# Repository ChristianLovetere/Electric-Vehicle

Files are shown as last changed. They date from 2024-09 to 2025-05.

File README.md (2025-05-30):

In this project, we use Dahlander motor technology via mechanical relays to alter the torque / speed of the electric vehicle. A custom PCB is used to route all the wiring connections from the Arduino MEGA to the RF Receiver, relays, battery, and motor / motor controllers.

<p align="center">
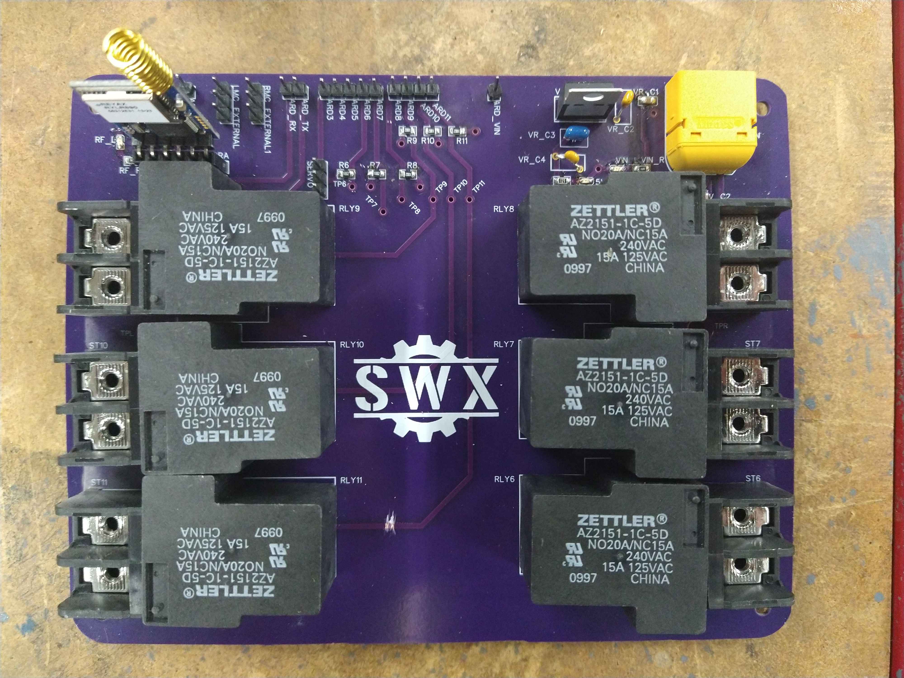
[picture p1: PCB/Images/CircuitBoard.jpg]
  
</p>

The PCB is a 4-layer design consisting of a Signal-Ground-Power-Signal stackup. The top and bottom (signal) layers can be seen below:

<p align="center">
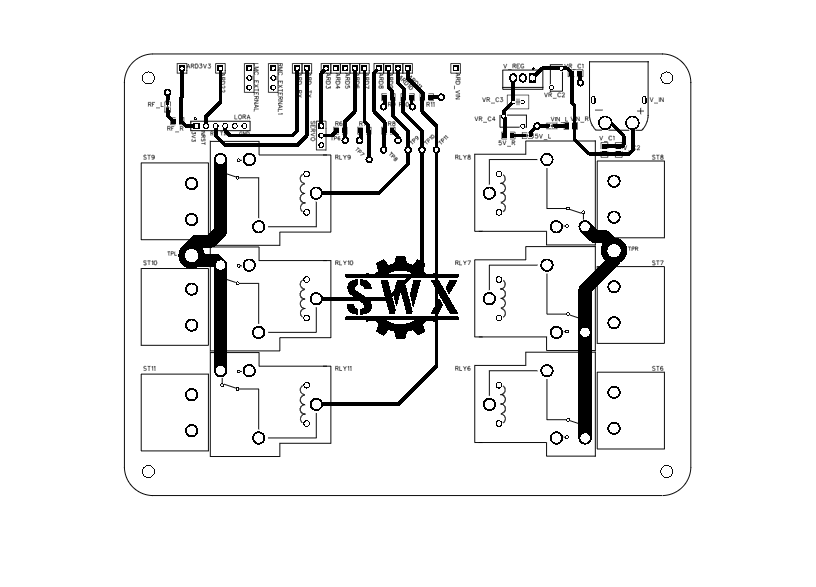
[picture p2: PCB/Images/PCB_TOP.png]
  
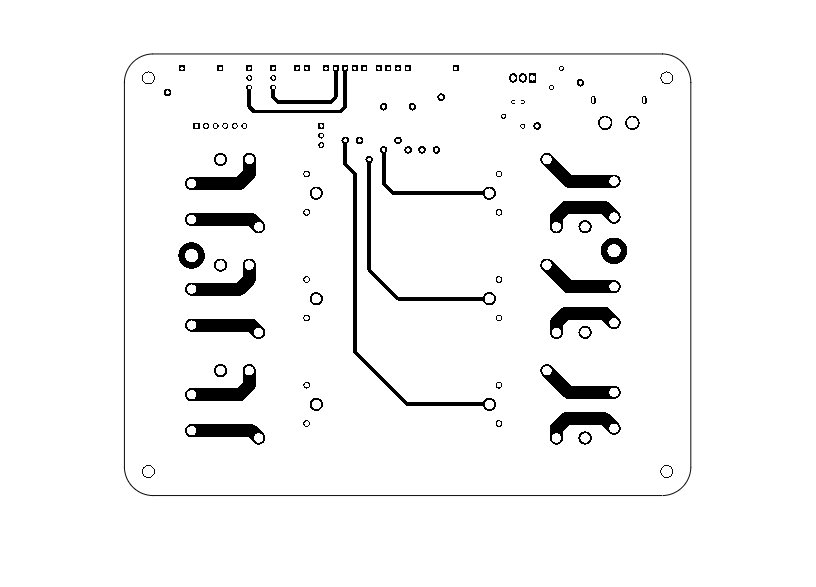
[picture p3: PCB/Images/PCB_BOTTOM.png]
  
</p>

This schematic shows the different aspects of the design. VCC is used to denote the power source (likely a 3S to 5S Lithium Polymer battery). A 7805L is used to drop the battery voltage down to 5V for delivery to the majority of the other components. The 3.3v required to power the REYAX RYLR896 (RF module) is acquired from the 3v3 pin on the Arduino, because the current supplied by this pin is enough to power the module without any trouble.
<p align="center">
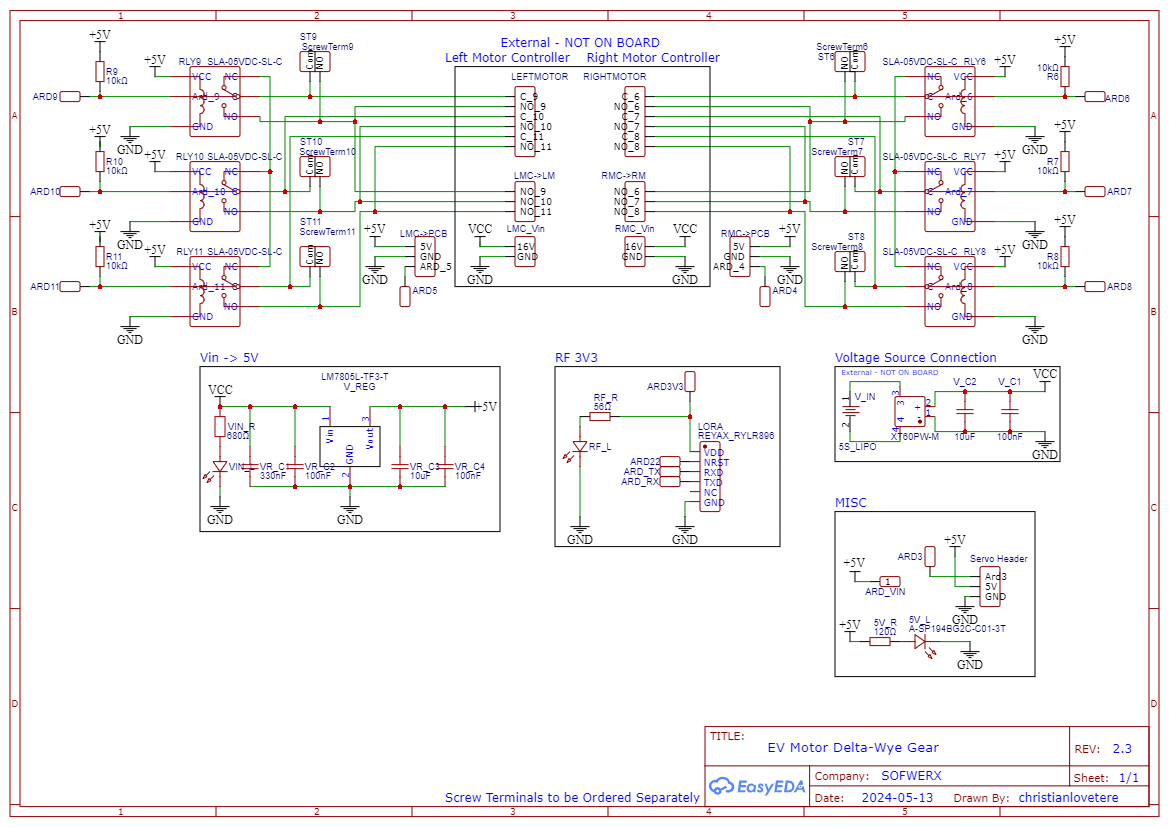
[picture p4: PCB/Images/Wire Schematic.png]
  
</p>

Portable Controller subproject has its own readme in the Portable Controller folder.

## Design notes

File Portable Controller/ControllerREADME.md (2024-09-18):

A subproject of the car project. This portable controller has a power on/off switch for ease of use and a USB-C charger slot so that it can be charged by any generic USB-C charger. It contains the REYAX RYLR896 RF module for transmitting to the Electric Vehicle, an HD44780 LCD screen with I2C backpack, raspberry pi 3, 5V 2.5A power bank, and a 3DConnexion SpaceMouse for input.

<p align="center">
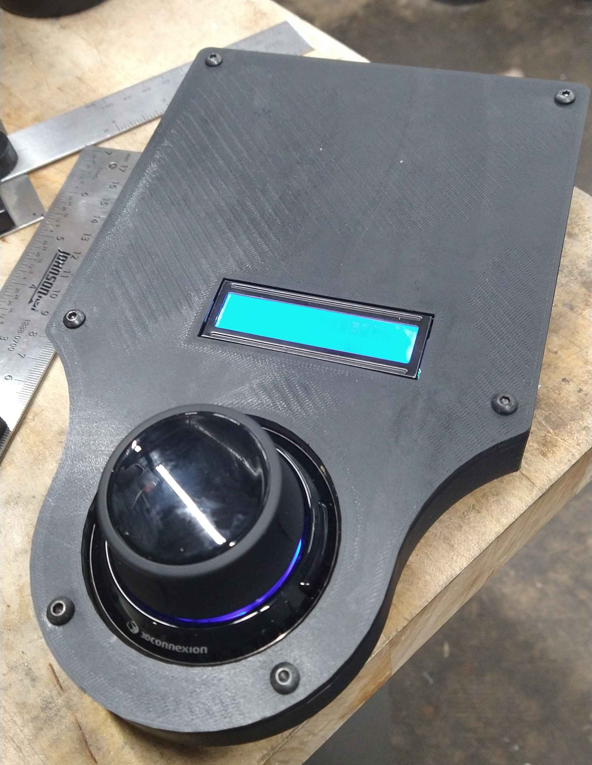
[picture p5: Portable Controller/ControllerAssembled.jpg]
  
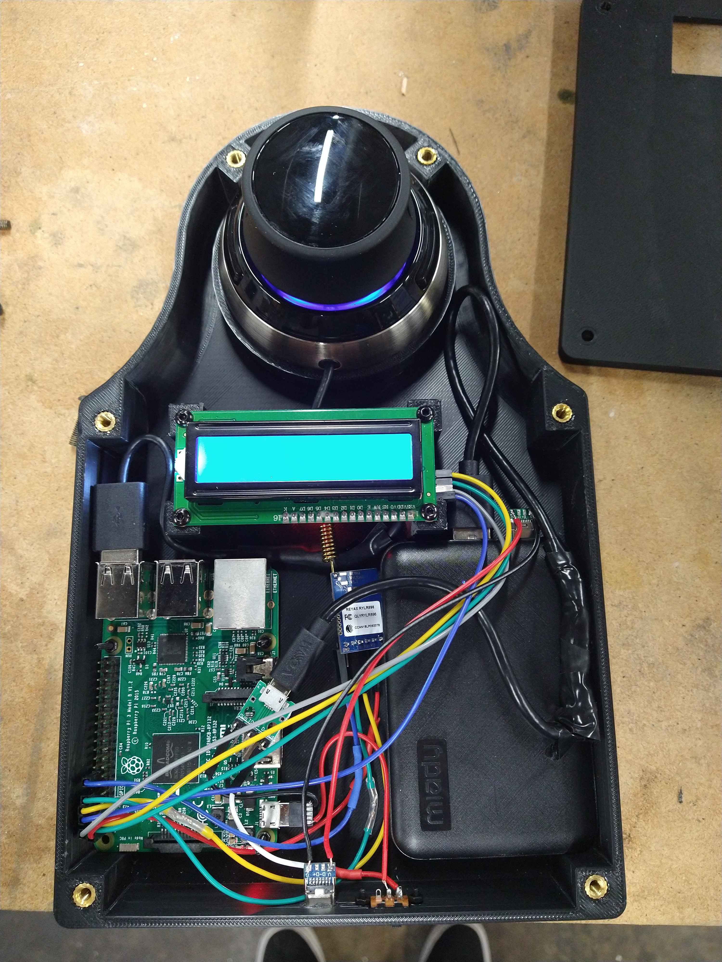
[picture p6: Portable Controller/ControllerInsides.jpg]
  
</p>

The LCD Screen displays the current left and right motor packet (intensity and direction) as well as a short string that demonstrates the intended action (slight left, hard right, drag turn, etc.)

The SpaceMouse is used to control the vehicle, rotating it left and right to indicate turning, and forward and backward for that. The side buttons are currently used to exit the program, but will eventually be used to flip the relays on the PCB and change gear for the vehicle.

Controller Schematic:

<p align="center">
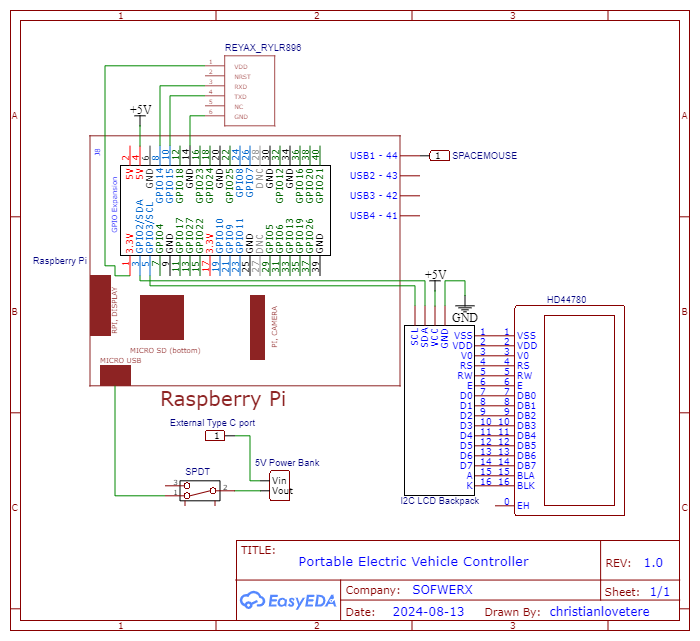
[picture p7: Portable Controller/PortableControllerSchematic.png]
What is this
  
</p>

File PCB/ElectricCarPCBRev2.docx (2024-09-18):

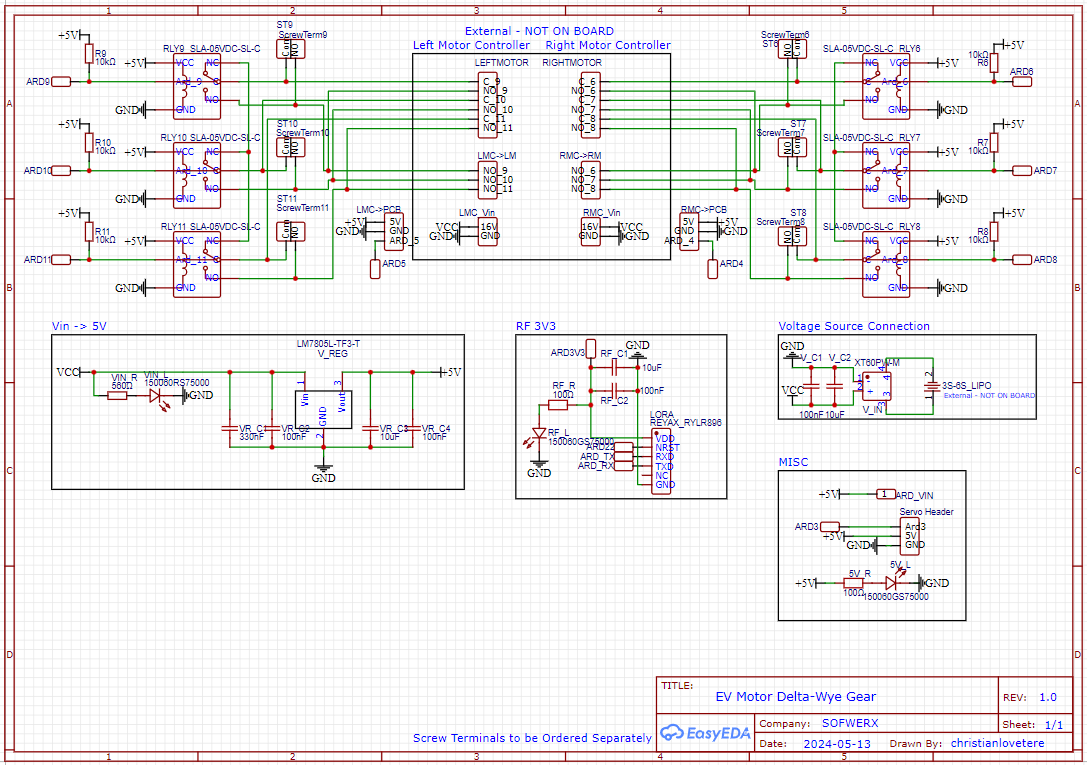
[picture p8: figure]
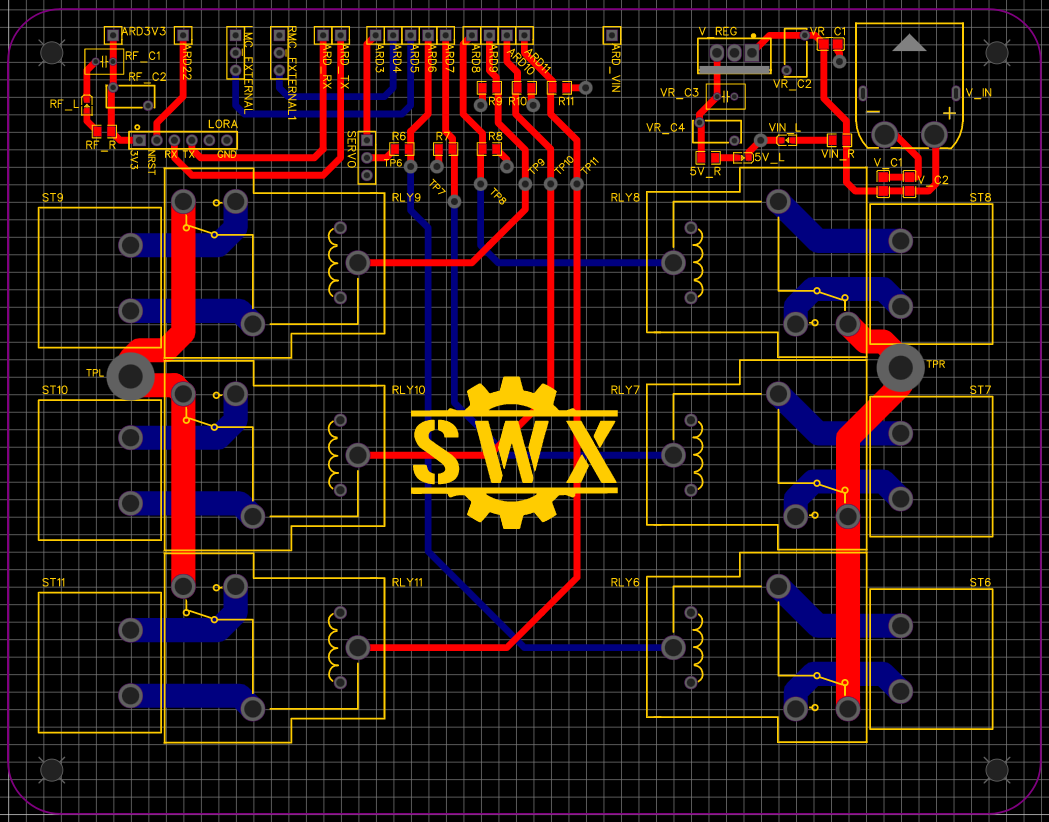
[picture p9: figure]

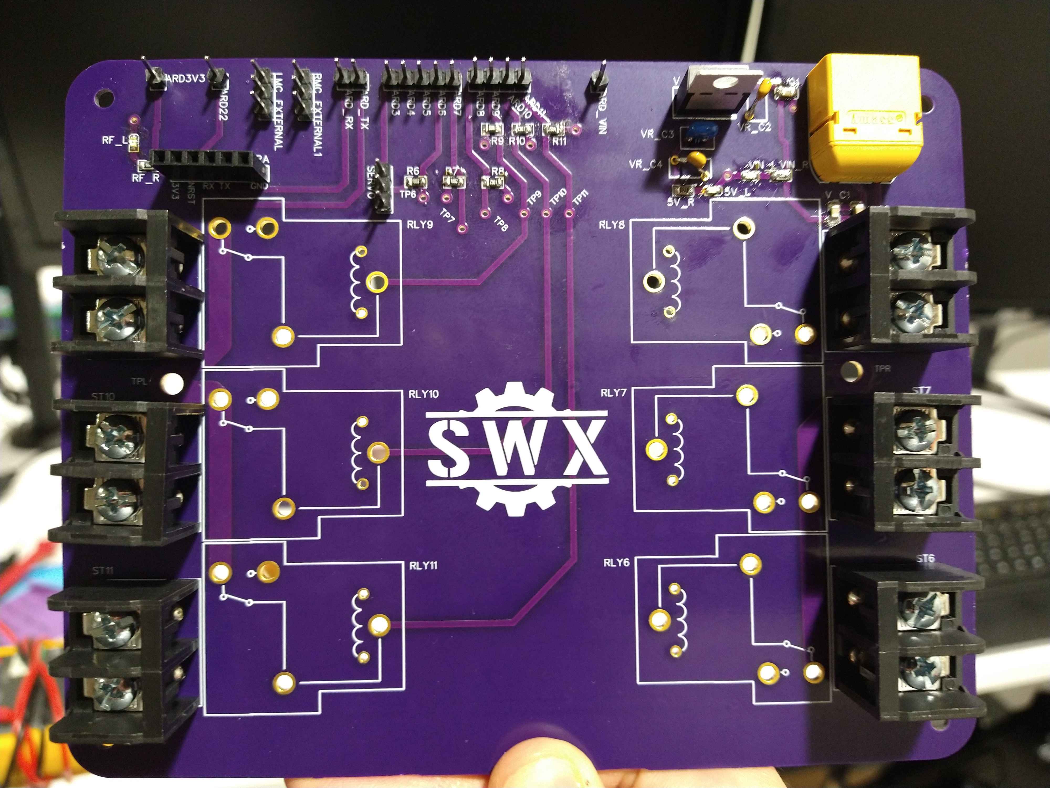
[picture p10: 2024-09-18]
PCB/Images/CircuitBoard2.jpg

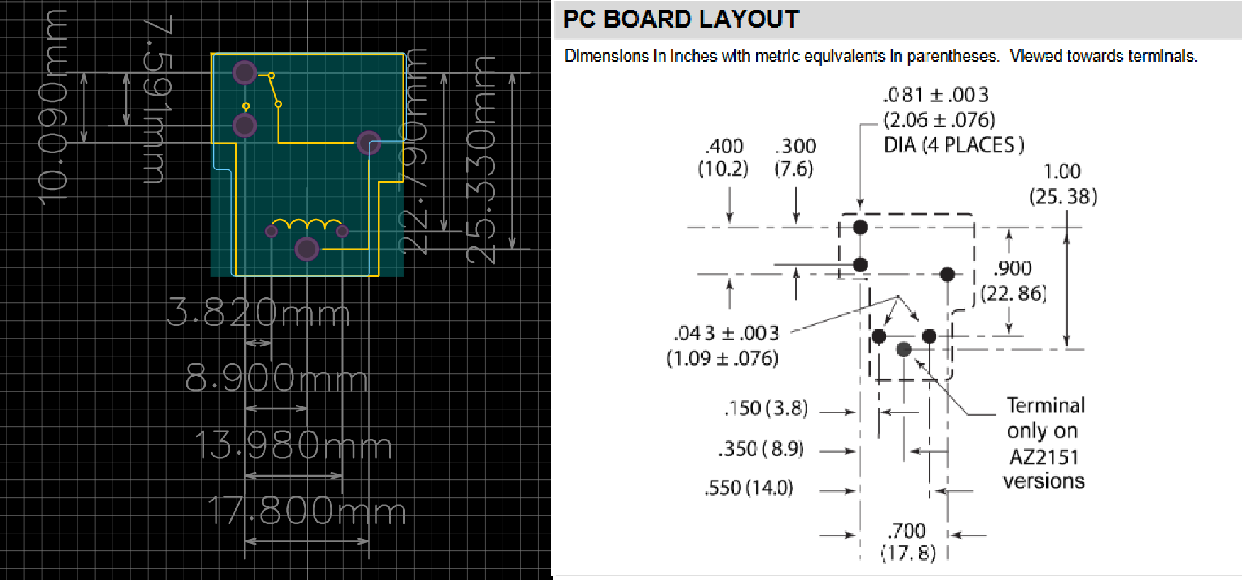
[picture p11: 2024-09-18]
Part Selection/american vs chinese relay.png

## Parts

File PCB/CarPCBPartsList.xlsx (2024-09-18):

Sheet: BOM_Electric-Car-PCB_2024-07-02
ID | Ordered | Replacement Found | Already Owned | On Board? | Name | Designator | Footprint | Quantity | Manufacturer Part | Manufacturer | Supplier | Supplier Part | Price | Link
1 |  |  | x |  | >16V | 5S_LIPO | BAT-SMD_CR1220-2 | 1 | CR1220-2 | Q&J | LCSC
2 | x |  |  | x | A-SP194BG2C-C01-3T | 5V_L,RF_L,VIN_L | LED0603-RD | 3 | A-SP194BG2C-C01-3T | Amicc(欧密格光电) | LCSC | C5179616 | 0.023 | https://jlcpcb.com/partdetail/Amicc-A_SP194BG2C_C013T/C5179616
3 |  | x |  | x | 120Ω | 5V_R | R0805 | 1 | RS-05K1200FT | FH(风华) | LCSC | C139926 | 0.002 | https://www.lcsc.com/datasheet/lcsc_datasheet_2304140030_FH--Guangdong-Fenghua-Advanced-Tech-RS-05K1200FT_C139926.pdf
4 |  | x |  | x | ARD3 | ARD3 | HDR-M-2.54_1X1 | 1 |  |  | LCSC | C81276 | 0.007 | -
5 |  | x |  | x | ARD3V3 | ARD3V3 | HDR-M-2.54_1X1 | 1 |  |  | LCSC | C81276 | 0.007 | -
6 |  | x |  | x | ARD4 | ARD4 | HDR-M-2.54_1X1 | 1 |  |  | LCSC | C81276 | 0.007 | -
7 |  | x |  | x | ARD5 | ARD5 | HDR-M-2.54_1X1 | 1 |  |  | LCSC | C81276 | 0.007 | -
8 |  | x |  | x | ARD6 | ARD6 | HDR-M-2.54_1X1 | 1 |  |  | LCSC | C81276 | 0.007 | -
9 |  | x |  | x | ARD7 | ARD7 | HDR-M-2.54_1X1 | 1 |  |  | LCSC | C81276 | 0.007 | -
10 |  | x |  | x | ARD8 | ARD8 | HDR-M-2.54_1X1 | 1 |  |  | LCSC | C81276 | 0.007 | -
11 |  | x |  | x | ARD9 | ARD9 | HDR-M-2.54_1X1 | 1 |  |  | LCSC | C81276 | 0.007 | -
12 |  | x |  | x | ARD10 | ARD10 | HDR-M-2.54_1X1 | 1 |  |  | LCSC | C81276 | 0.007 | -
13 |  | x |  | x | ARD11 | ARD11 | HDR-M-2.54_1X1 | 1 |  |  | LCSC | C81276 | 0.007 | -
14 |  | x |  | x | ARD22 | ARD22 | HDR-M-2.54_1X1 | 1 |  |  | LCSC | C81276 | 0.007 | -
15 |  | x |  | x | ARD_RX | ARD_RX | HDR-M-2.54_1X1 | 1 |  |  | LCSC | C81276 | 0.007 | -
16 |  | x |  | x | ARD_TX | ARD_TX | HDR-M-2.54_1X1 | 1 |  |  | LCSC | C81276 | 0.007 | -
17 |  | x |  | x | ARD_VIN | ARD_VIN | HDR-M-2.54_1X1 | 1 |  |  | LCSC | C81276 | 0.007 | -
18 |  |  |  |  | LEFTMOTOR | LEFTMOTOR | HDR-M-2.54_1X6 | 1 |  |  | LCSC | C190819 | 0.029
19 |  |  |  |  | LMC_Vin | LMCPOWER | HDR-M-2.54_1X2 | 1 |  |  | LCSC | C124375 | 0.023
20 |  | x |  | x | LMC->PCB | LMC_EXTERNAL | HDR-M-2.54_1X3 | 1 |  |  | LCSC | C180248 | 0.181 | -
21 |  |  |  |  | LMC->LM | LMC_INTERNAL | HDR-M-2.54_1X3 | 1 |  |  | LCSC | C180248 | 0.181
22 |  |  | x | x | REYAX_RYLR896 | LORA | HDR-TH_6P-P2.54-V-F | 1 | 2.54-1*6P母 | BOOMELE(博穆精密) | LCSC | C40877 | 0.071
23 | x |  |  | x | 10kΩ | R6,R7,R8,R9,R10,R11 | R0805 | 6 | RC0805FR-0710KL | YAGEO(国巨) | LCSC | C84376 | 0.002 | https://www.digikey.com/en/products/detail/yageo/RC0805FR-0710KL/727535
24 | x |  |  | x | 56Ω | RF_R | R0805 | 1 | 0805W8J0560T5E | UNI-ROYAL(厚声) | LCSC | C25320 | 0.001 | https://www.lcsc.com/product-detail/Chip-Resistor-Surface-Mount_Uniroyal-Elec-0805W8J0560T5E_C25320.html
25 |  |  |  |  | RIGHTMOTOR | RIGHTMOTOR | HDR-M-2.54_1X6 | 1 |  |  | LCSC | C190819 | 0.029
26 |  | x |  | x | SLA-05VDC-SL-C | RLY6,RLY7,RLY8,RLY9,RLY10,RLY11 | RELAY-TH_SLA-XXVDC-XX-C | 6 | SLA-05VDC-SL-C | 松乐 | LCSC | C87367 | 0.928 | https://www.lcsc.com/product-detail/Power-Relays_Ningbo-Songle-Relay-SLA-05VDC-SL-C_C87367.html
27 |  |  |  |  | RMC_Vin | RMCPOWER | HDR-M-2.54_1X2 | 1 |  |  | LCSC | C124375 | 0.023
28 |  | x |  | x | RMC->PCB | RMC_EXTERNAL1 | HDR-M-2.54_1X3 | 1 |  |  | LCSC | C180248 | 0.181 | -
29 |  |  |  |  | RMC->RM | RMC_INTERNAL1 | HDR-M-2.54_1X3 | 1 |  |  | LCSC | C180248 | 0.181
30 |  | x |  | x | Servo Header | SERVO | HDR-M-2.54_1X3 | 1 |  |  | LCSC | C180248 | 0.181 | -
31 | x |  |  | x | ScrewTerm6 | ST6 | TERMINAL_BLOCK_2 | 1 | 6PCV-02-006 |  | LCSC | C124375 | 0.023 | https://www.digikey.com/en/products/detail/te-connectivity-amp-connectors/6PCV-02-006/1277933
32 | x |  |  | x | ScrewTerm7 | ST7 | TERMINAL_BLOCK_2 | 1 | 6PCV-02-006 |  | LCSC | C124375 | 0.023 | https://www.digikey.com/en/products/detail/te-connectivity-amp-connectors/6PCV-02-006/1277934
33 | x |  |  | x | ScrewTerm8 | ST8 | TERMINAL_BLOCK_2 | 1 | 6PCV-02-006 |  | LCSC | C124375 | 0.023 | https://www.digikey.com/en/products/detail/te-connectivity-amp-connectors/6PCV-02-006/1277935
34 | x |  |  | x | ScrewTerm9 | ST9 | TERMINAL_BLOCK_2 | 1 | 6PCV-02-006 |  | LCSC | C124375 | 0.023 | https://www.digikey.com/en/products/detail/te-connectivity-amp-connectors/6PCV-02-006/1277936
35 | x |  |  | x | ScrewTerm10 | ST10 | TERMINAL_BLOCK_2 | 1 | 6PCV-02-006 |  | LCSC | C124375 | 0.023 | https://www.digikey.com/en/products/detail/te-connectivity-amp-connectors/6PCV-02-006/1277937
36 | x |  |  | x | ScrewTerm11 | ST11 | TERMINAL_BLOCK_2 | 1 | 6PCV-02-006 |  | LCSC | C124375 | 0.023 | https://www.digikey.com/en/products/detail/te-connectivity-amp-connectors/6PCV-02-006/1277938
37 | x |  |  | x | 680Ω | VIN_R | R0805 | 1 | CR0805F680RP05Z | EVER OHMS(天二科技) | LCSC | C880974 | 0.003 | https://jlcpcb.com/kr/partdetail/Ever_OhmsTech-CR0805F680RP05Z/C880974
38 | x |  |  | x | 330nF | VR_C1 | C0805 | 1 | GCJ219R71H334KA12D | muRata(村田) | LCSC | C527609 | 0.091 | https://www.digikey.com/en/products/detail/murata-electronics/GCJ219R71H334KA12D/6606042
39 |  | x |  | x | 100nF | VR_C2,VR_C4 | CAP-TH_L7.0-W3.2-P5.08-D0.6-S2.7 | 2 | CC2A104ZC1ED3F7C1100 | Dersonic(德尔创) | LCSC | C2761731 | 0.02 | https://www.lcsc.com/product-detail/Ceramic-Disc-Capacitors_Dersonic-CC2A104ZC1ED3F7C1100_C2761731.html
 | x |  |  | x | 10uF | VR_C3 | CAP-TH_L5.5-W3.5-P2.50-D0.5 | 1 | FK16X7R1C106K | TDK | LCSC | C3689076 | 0.142 | https://www.digikey.com/en/products/detail/tdk-corporation/FK16X7R1C106KR020/2815278
41 | x |  |  | x | 100nF | V_C1 | C0805 | 1 | CC0805KRX7R8BB104 | YAGEO(国巨) | LCSC | C519981 | 0.006 | https://www.digikey.com/en/products/detail/yageo/CC0805KRX7R8BB104/302875
42 |  | x |  | x | 10uF | V_C2 | C0805 | 1 | TCC0805X5R106K100FT | CCTC(三环) | LCSC | C380331 | 0.009 | https://jlcpcb.com/partdetail/CCTC-TCC0805X5R106K100FT/C380331
43 | x |  |  | x | XT60PW-M | V_IN | CONN-TH_XT60PW-M | 1 | XT60PW-M | AMASS(艾迈斯) | LCSC | C98732 | 0.388 | https://www.tme.com/us/en-us/details/xt60pw-m/dc-power-connectors/amass/
44 | x |  | x | x | LM7805L-TF3-T | V_REG | TO-220F-3_L10.2-W4.9-P2.54-L | 1 | LM7805L-TF3-T | UTC(友顺) | LCSC | C71107 | 0.216 | https://www.digikey.com/en/products/base-product/onsemi/488/LM7805/17942

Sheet: Digikey Part Replacements
Old Part | New Part Link | Quantity | Works For
HDR-M-2.54_1X1 | https://www.digikey.com/en/products/detail/w%C3%BCrth-elektronik/61300111121/4846821 | 3 | ARD3V3, ARD22, ARD_VIN
HDR-M-2.54_1X2 | https://www.digikey.com/en/products/detail/w%C3%BCrth-elektronik/61300211121/4846823 | 1 | ARD_RX, ARD_TX
HDR-M-2.54_1X3 | https://www.digikey.com/en/products/detail/w%C3%BCrth-elektronik/61300311121/4846825 | 3 | LMC_External, RMC_External, Servo Header
HDR-M-2.54_1X4 | https://www.digikey.com/en/products/detail/w%C3%BCrth-elektronik/61300411121/4846827 | 1 | ARD8-11
HDR-M-2.54_1X5 | https://www.digikey.com/en/products/detail/w%C3%BCrth-elektronik/61300511121/4846831 | 1 | ARD3-7
CC2A104ZC1ED3F7C1100 | https://www.digikey.com/en/products/detail/vishay-beyschlag-draloric-bc-components/K104K10X7RF5UH5/2356754 | 2 | VR_C2, VR_C4
TCC0805X5R106K100FT | https://www.digikey.com/en/products/detail/cal-chip-electronics-inc/GMC21X7R106K25NT/22639515 | 1 | V_C2
SLA-05VDC-SL-C | https://www.e-sonic.com/en/productdetail/american-zettler/az21511a5de-10610544.html | 6 | RLY6-11
 | https://www.masterelectronics.com/en/productdetail/american-zettler/az21511a5de-10610544.html
RS-05K1200FT | https://www.digikey.com/en/products/detail/susumu/RG2012N-121-W-T1/600666 | 1 | 5V_R

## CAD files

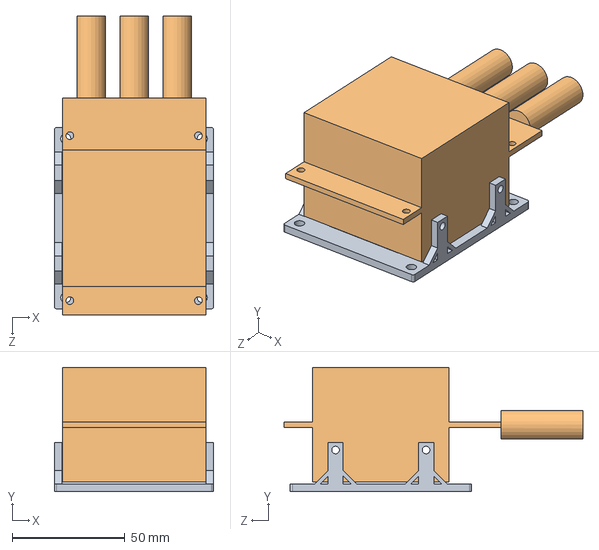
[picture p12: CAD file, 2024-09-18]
3D Modeling/MotorControllerFit.SLDASM
70.4 x 55.1 x 132.4 mm
MotorController
MotorControllerMount

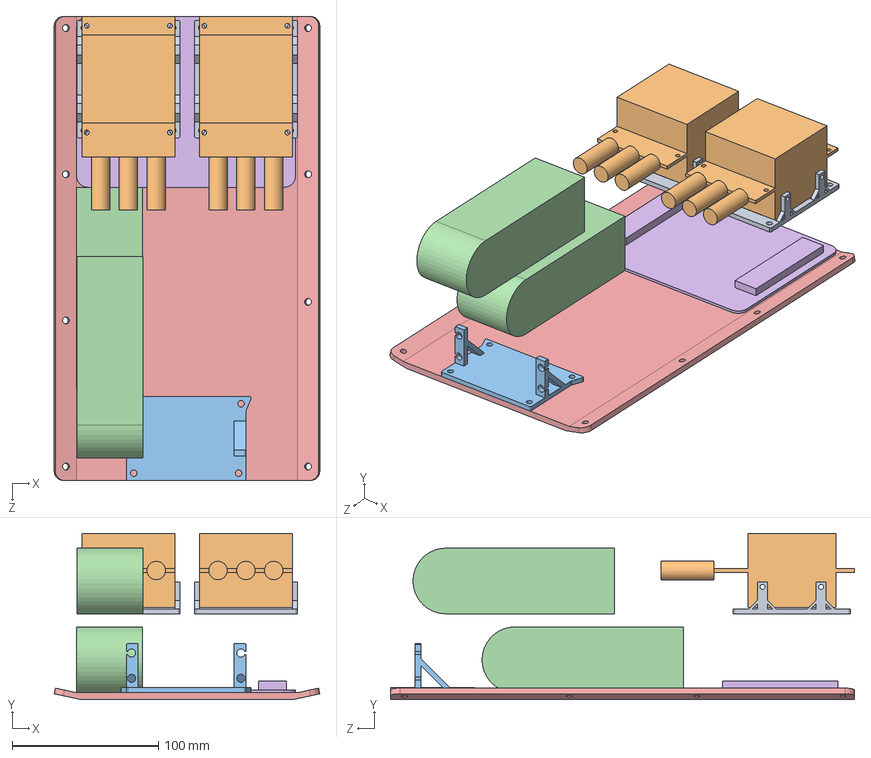
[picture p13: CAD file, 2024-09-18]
3D Modeling/ElecCarAssembly.SLDASM
181.8 x 113.8 x 317.5 mm
PCB
VehicleBase
6s LiPo x 2
ServoMount
MotorController x 2
MotorControllerMount x 2

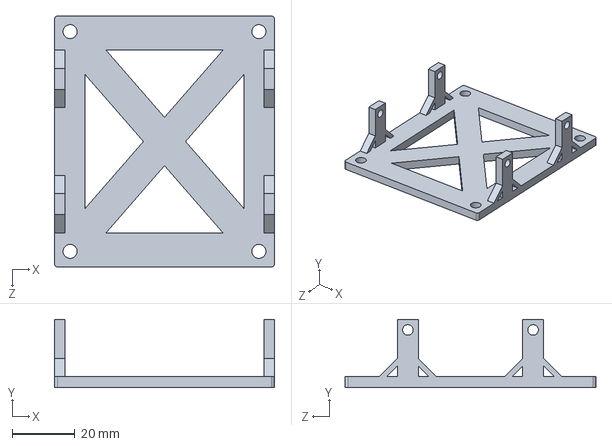
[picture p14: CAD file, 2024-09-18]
3D Modeling/MotorControllerMount.SLDPRT
70.4 x 21.9 x 80.3 mm

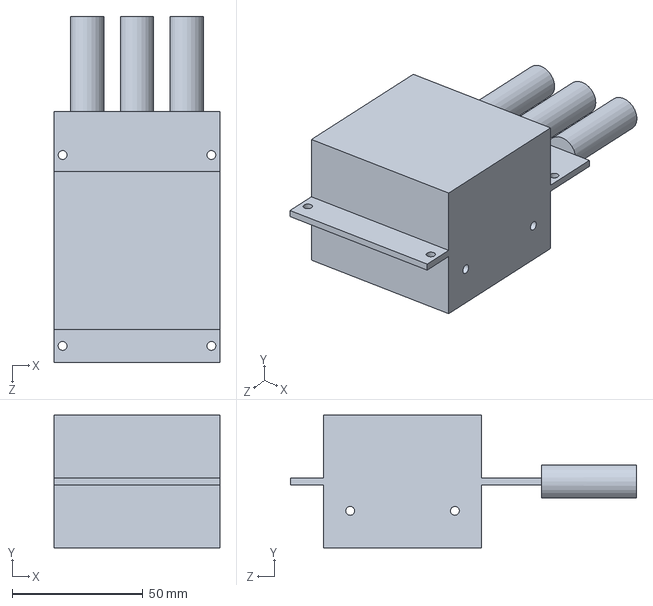
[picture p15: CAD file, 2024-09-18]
3D Modeling/MotorController.SLDPRT
63.5 x 50.8 x 132.4 mm

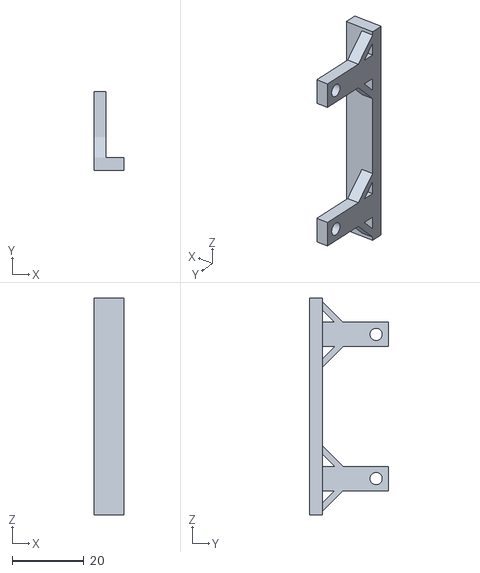
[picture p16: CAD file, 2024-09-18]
3D Modeling/MotorControllerMountTESTPART_2.STL
8.38 x 21.9 x 60.3

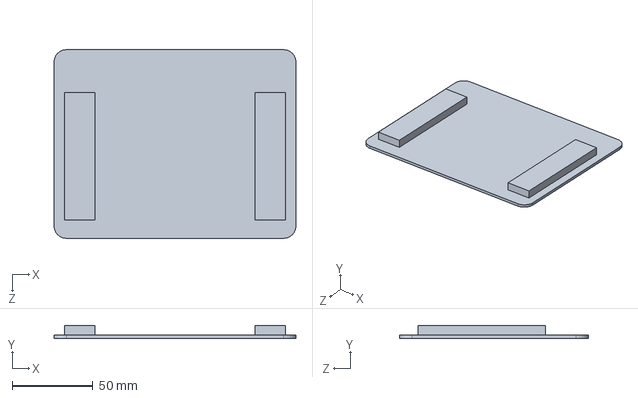
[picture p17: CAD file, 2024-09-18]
3D Modeling/PCB.SLDPRT
149.9 x 7.84 x 116.8 mm

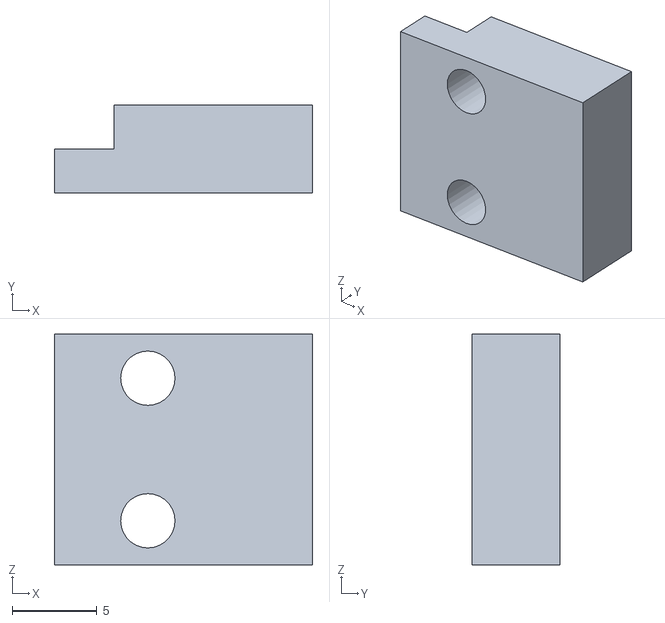
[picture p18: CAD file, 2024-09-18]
3D Modeling/micro usb pin cover.stl
15.2 x 5.20 x 13.6

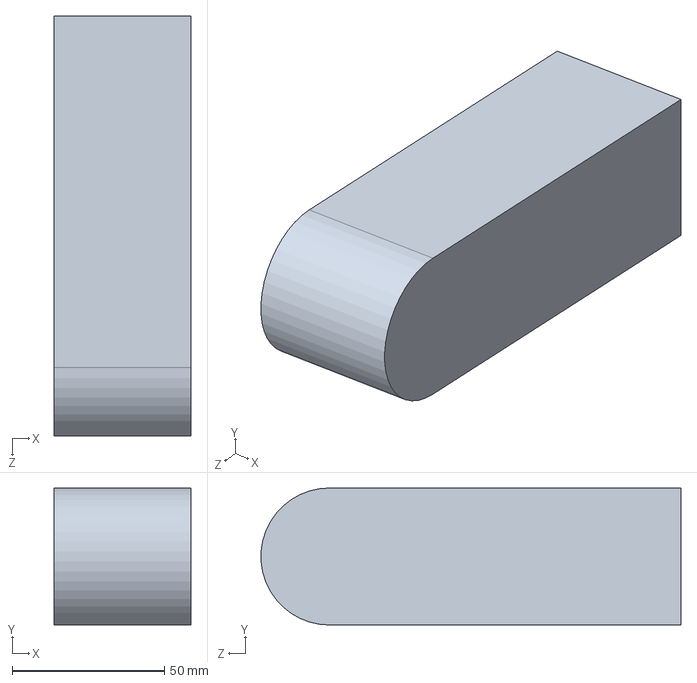
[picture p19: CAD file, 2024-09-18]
3D Modeling/6s LiPo.SLDPRT
45.0 x 45.0 x 137.9 mm

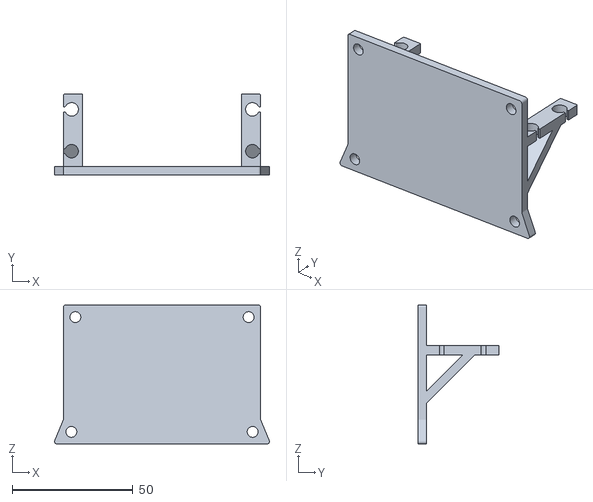
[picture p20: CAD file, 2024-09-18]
3D Modeling/ServoMountMK2.STL
89.0 x 33.5 x 57.5

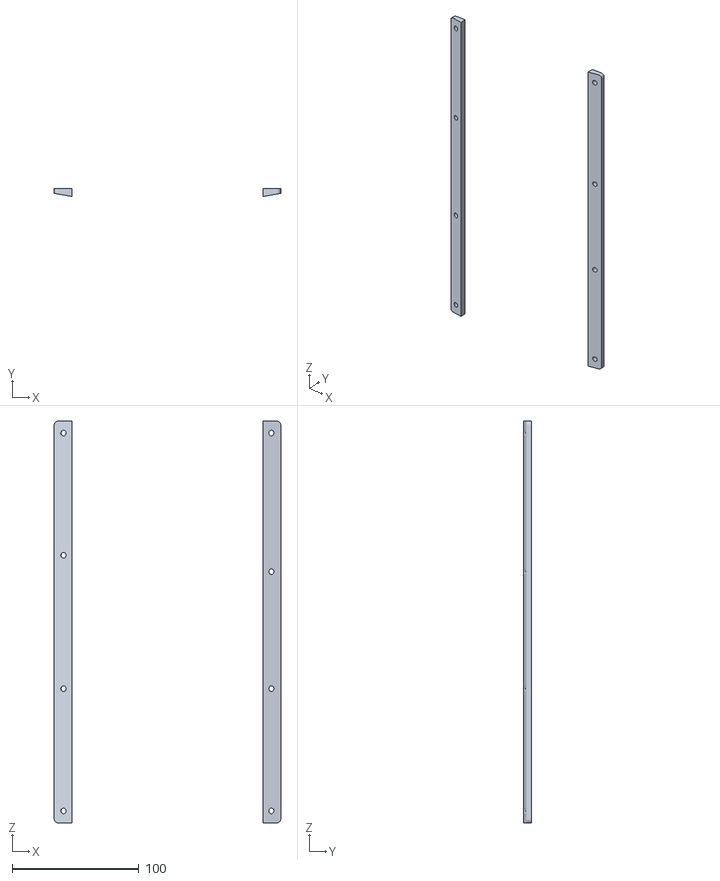
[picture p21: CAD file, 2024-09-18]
3D Modeling/VehicleChassisHoleAlignmentTestPart.STL
179.0 x 6.35 x 317.5

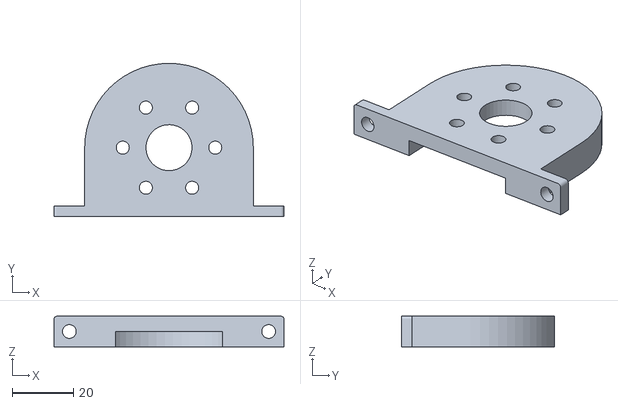
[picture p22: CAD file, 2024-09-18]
3D Modeling/MotorMountTESTPART_2.STL
75.0 x 50.0 x 10.0

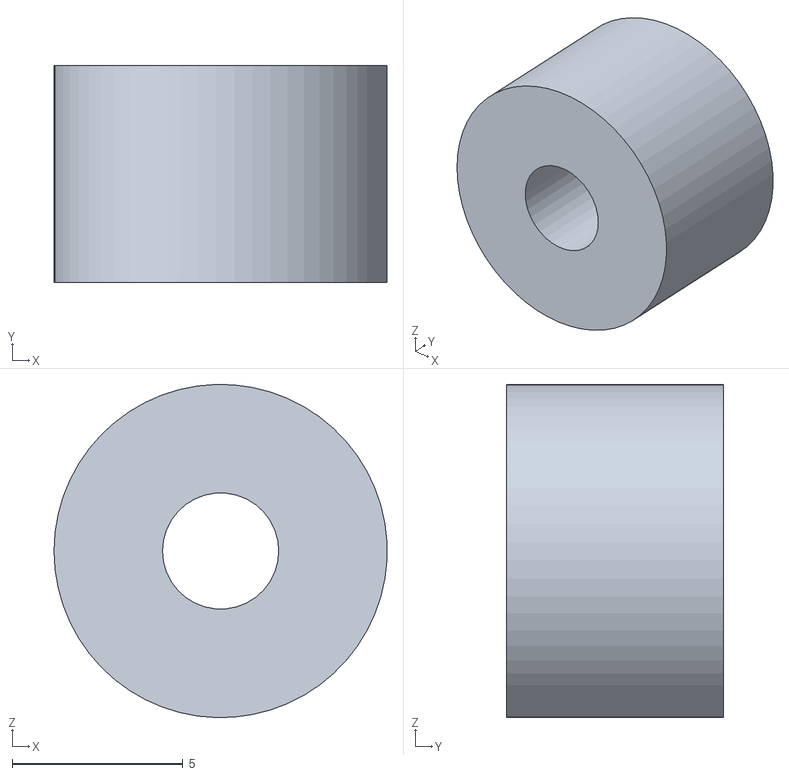
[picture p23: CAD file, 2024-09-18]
3D Modeling/spacer for mounting pcb.stl
9.74 x 6.35 x 9.75

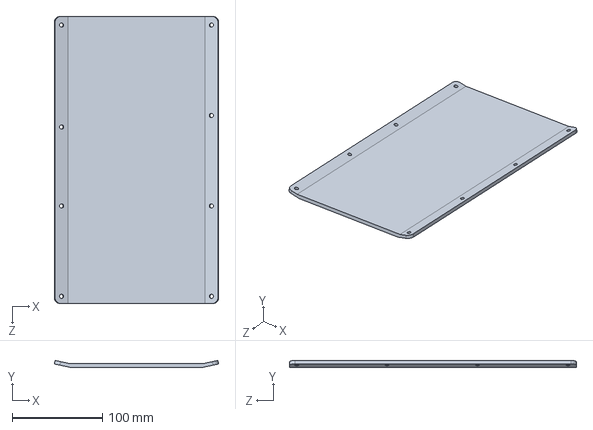
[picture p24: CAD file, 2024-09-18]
3D Modeling/VehicleBase.SLDPRT
181.8 x 7.89 x 317.5 mm

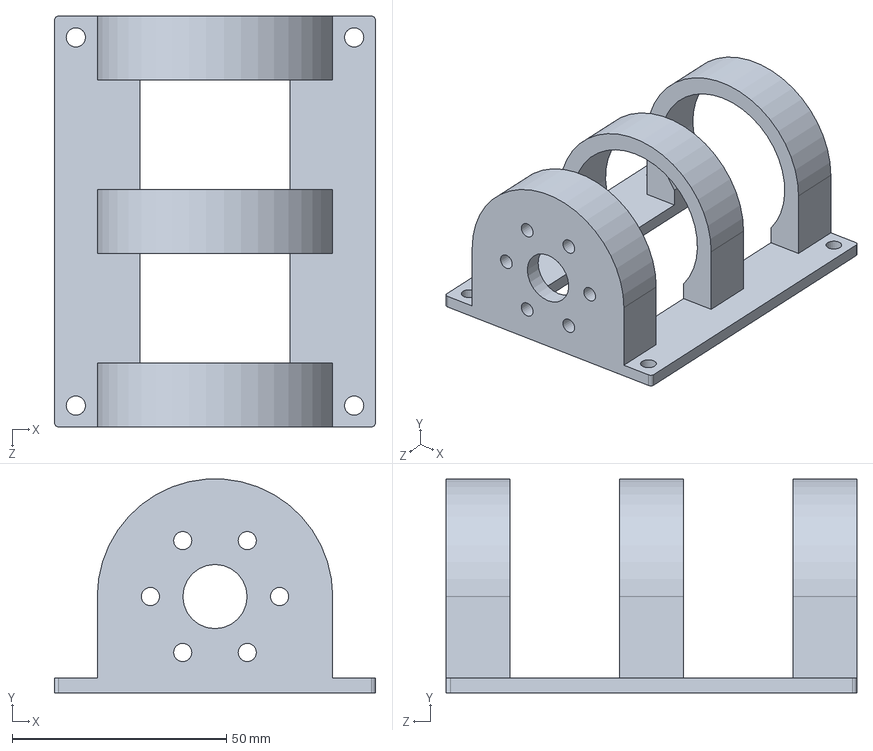
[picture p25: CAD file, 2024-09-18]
3D Modeling/MotorMount.SLDPRT
75.0 x 49.9 x 96.0 mm

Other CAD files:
3D Modeling/ServoMount.SLDPRT
3D Modeling/c-3-1437652-9-p-3d.SLDPRT
3D Modeling/Car Controller.SLDPRT
3D Modeling/MotorControllerMountFINAL.STL
3D Modeling/MotorMount.STL
3D Modeling/MotorMountFINAL.STL
3D Modeling/OldVersions/micro usb pin cover.0002.ipt
3D Modeling/ServoMount.STL
3D Modeling/VehicleChassis.SLDPRT
3D Modeling/micro usb pin cover.ipt
3D Modeling/spacer for mounting pcb.ipt

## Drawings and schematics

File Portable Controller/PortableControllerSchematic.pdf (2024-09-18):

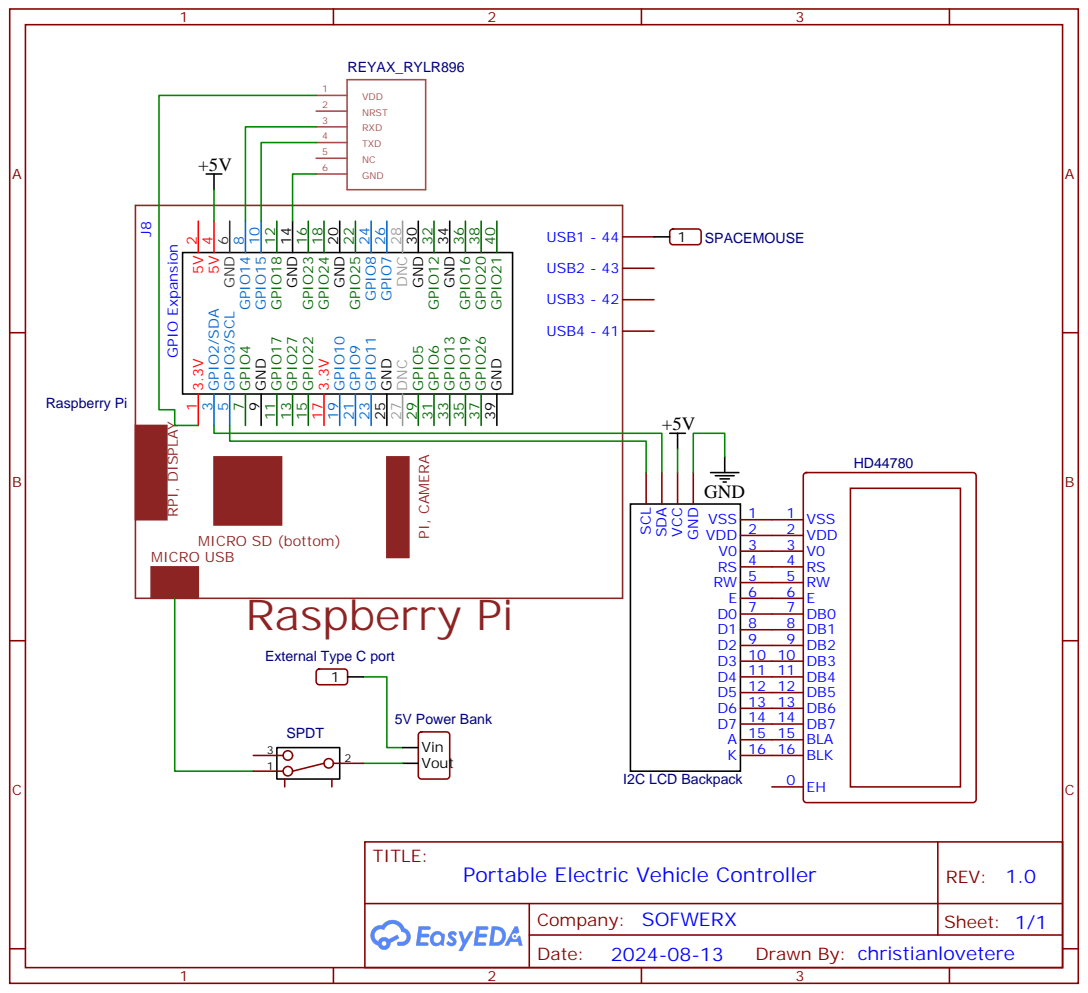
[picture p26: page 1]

MICRO USB RPI, DISPLAY

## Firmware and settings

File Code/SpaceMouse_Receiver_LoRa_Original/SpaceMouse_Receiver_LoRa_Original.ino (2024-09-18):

/* Receiver code for the Arduino Radio control with PWM output
 * Connect a NRF24 module to it:
 
    Module // Arduino Mega
    
    GND    ->   GND
    Vcc    ->   3.3V
    CE     ->   D48
    CSN    ->   D49
    SCK    ->   D52
    MOSI   ->   D51
    MISO   ->   D50

This code receive 3 channels and create a PWM output for each one on D3, D4, D5
*/
#include<SPI.h>                   // spi library for connecting nrf
#include<RF24.h>                  // nrf library
#include "printf.h"
#include <Servo.h>

Servo escR;
Servo escL;
Servo myServo;

int ch1_value = 0;
int ch2_value = 0;
int ch3_value = 0;
unsigned long lastRecvTime = 0;

 int unpacked_data[3]; // Using int16_t for 2-byte signed integers

void reset_the_Data() 
{
  // 'safe' values to use when NO radio input is detected
  // ch1_value = 1500;
  // ch2_value = 1500;
  // ch3_value = 1500;
}

void setup(void) {

  while (!Serial);

  pinMode(53, OUTPUT);
  pinMode(46, OUTPUT);
  printf_begin();

 Serial.println("Ready to Receive") ;

 reset_the_Data();

  myServo.attach(3); //pin3 sends steering PWM to Servo
  escL.attach(4);    //pin4 is sends motor PWM to left motor
  escR.attach(5);   //pin5 is sends motor PWM to right motor


   // put your setup code here, to run once:

  //pinMode(rxPin, INPUT);
  //pinMode(txPin, OUTPUT);
  delay(1000);
  Serial.begin(115200);
  //Serial.end();
  
  //serial1.begin(115200);
  delay(250);
  Serial.print("AT\r\n");
  //Serial.flush();
  delay(250);
  Serial.print("AT+PARAMETER=7,9,4,7\r\n");
  //Serial.flush();
  delay(250);
  Serial.print("AT+NETWORKID=6\r\n");
  //Serial.flush();
  delay(250);
  Serial.print("AT+ADDRESS=1\r\n");
  //Serial.flush();
  delay(250);
  Serial.print("AT+PARAMETER?\r\n");
  //Serial.flush();
  delay(250);
  Serial.print("AT+NETWORKID?\r\n");
  //Serial.flush();
  delay(250);
  Serial.print("AT+ADDRESS?\r\n");
  //Serial.flush();
  delay(250);
  //Serial.end();
}


void loop(void) {


  // Wait for a response from the module
  //delay(2000);  // Longer delay to allow processing

  // Read and print the response
  String data = "";
  while (Serial.available()) {
    char c = Serial.read();
    data += c;
    //Serial.print(c);
  }
  //Serial.print(data);
  //Serial.flush();



    int index0 = data.indexOf("@");
    int index1 = data.indexOf("#");
    int index2 = data.indexOf("$");
    int index3 = data.indexOf("%");
    String data0 = (data.substring(index0+1, index1));
    String data1 = (data.substring(index1+1, index2));
    String data2 = (data.substring(index2+1, index3));
    unpacked_data[0] = data0.toInt();
    unpacked_data[1] = data1.toInt();
    unpacked_data[2] = data2.toInt();
    ch1_value = map(unpacked_data[0],-350,350,800,2000);
    ch2_value = map(unpacked_data[1], -350,350,1000,2000);
    ch3_value = map(unpacked_data[2],-350,350,1000,2000);
    lastRecvTime = millis(); //Here we receive the data
    //Serial.println("Data Received");
 

   Serial.println(data0+" "+data1+" "+data2);
   Serial.print(ch1_value);
   Serial.print(" ");
   Serial.print(ch2_value);
   Serial.print(" ");
   Serial.print(ch3_value);
   Serial.println(" ");
  
  myServo.write(ch1_value);
  escL.write(ch2_value);
  escR.write(ch3_value);

  // Reset the module (if needed)
  digitalWrite(22, LOW);
   delay(100);
   digitalWrite(22, HIGH);

}

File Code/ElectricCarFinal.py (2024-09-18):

#!/usr/bin/env python
#input from spacemouse sends 3 variables from rpi to arduino
#transmitter code
#pi@raspberrypi:~/Desktop/Dahlander_Motor $ sudo python SpaceMouse_Transmitter_Final.py


import RPi.GPIO as GPIO
import time
import spidev
spi = spidev.SpiDev()
spi.open(0,1)
import sys
import struct
import usb
import usb.core
import usb.util

from time import gmtime, strftime
import time
import serial

#instantiate serial channel 
ser = serial.Serial('/dev/ttyS0', baudrate=115200)
def setup():
    GPIO.setmode(GPIO.BCM)                   # set the gpio mode

    #List of all the commands we want to run for reyax setup
    listToBeWrittenToSerial = [b'AT+PARAMETER=7,9,4,7\r\n', b'AT+NETWORKID=6\r\n',
                               b'AT+ADDRESS=0\r\n', b'AT+PARAMETER?\r\n', b'AT+NETWORKID?\r\n',
                               b'AT+ADDRESS?\r\n', b'AT+IPR?\r\n']

    print('##########Setup Phase##########')
    #for loop that writes each command, waits a sec, then prints reyax's response
    for command in listToBeWrittenToSerial: #for all strings in the list
        decodedCommand = command.decode('utf-8') #create decoded command
        cleanCommand = decodedCommand.replace("AT+", "").replace("\r\n", "") #readable version of the command
        try:
            ser.write(command) #write command to serial line
            time.sleep(0.2) #wait 200ms
            response = ser.read_all().decode() #get Reyax's response
            print("from", cleanCommand, "| Reyax RYLR896 says:", response) #readable feedback during code execution
        except UnicodeDecodeError: #throw out data if a decoding error happens
            print("Data corrupted. Could not decode ", command, ".")

    time.sleep(1)

def main(args):

    setup()
    # Look for SpaceNavigator
    dev = usb.core.find(idVendor=0x256f, idProduct=0xc635)

    cfg = dev.get_active_configuration()
    intf = cfg[(0,0)]
    ep = usb.util.find_descriptor(intf, custom_match = lambda e: usb.util.endpoint_direction(e.bEndpointAddress) == usb.util.ENDPOINT_IN)
    
    reattach = False
    if dev.is_kernel_driver_active(0):
        reattach = True
        dev.detach_kernel_driver(0)
    
    ep_in = dev[0][(0,0)][0]
    ep_out = dev[0][(0,0)][1]
    
    print ('Exit by pressing any button on the SpaceNavigator\n')
    time.sleep(1)

###########################

    rz = 0
    motLeft = 0
    motRight = 0
    
    run = True
    while run :
        try:
            data = dev.read(int(ep_in.bEndpointAddress), int(ep_in.bLength), 0)
            #print data
    
            if data[0] == 1:
                # translation packet
                tx = data[1] + (data[2]*256)
                ty = data[3] + (data[4]*256)
                tz = data[5] + (data[6]*256)
                
                if data[2] > 127:
                    tx -= 65536
                if data[4] > 127:
                    ty -= 65536
                if data[6] > 127:
                    tz -= 65536
    
            if data[0] == 2:
                # rotation packet
                rx = data[1] + (data[2]*256)
                ry = data[3] + (data[4]*256)
                rz = data[5] + (data[6]*256)
                
                if data[2] > 127:
                    rx -= 65536
                if data[4] > 127:
                    ry -= 65536
                if data[6] > 127:
                    rz -= 65536
    
                
            if data[0] == 3 and data[1] == 0:
                # button packet - exit on the release
                run = False
                
    
            #motor
            # -ty controls forward movement, +ty backwards
            # -rz turns right, rz turns left
            motRight = -ty - rz/4;              #rz/x changes degree of steering 
            motLeft = -ty + rz/4;
            if motRight > 350:
               motRight = 350;
            if motRight < -350:
               motRight = -350;
            if motLeft > 350:
               motLeft = 350;
            if motLeft < -350:
               motLeft = -350;

            try:
                c1 = 'AT+SEND=1,' #first segment of message
                SMdata = "@"+str(int(rz))+"#"+str(int(motLeft))+"$"+str(int(motRight))+"%" #third segment of message - Mouse data enclosed with parsing identifiers
                lengthOfSMdata = str(len(SMdata)) #second segment of message
                c2 = '\r\n' #fourth segment of message

                fullMessage = c1+lengthOfSMdata+","+SMdata+c2 #Full unencoded string for command
                encodedMessage = fullMessage.encode("utf-8") #encode message to utf-8

                cleanMessage = fullMessage.replace("AT+", "").replace("\r\n", "") #readable version of the unencoded message
                ser.write(encodedMessage) #send encoded message to serial
                time.sleep(0.10) #wait 100ms
                response = ser.read_all().decode() #read reyax's response to the command we sent
                print("from", cleanMessage, "| Reyax RYLR896 says:", response) #readable feedback during code execution
            except UnicodeDecodeError: #if a decoding error occurs, that message is not sent
                print("Data corrupted. Skipping data.")

        except usb.core.USBError:
             print("USB error")
             run = False
        except Exception as e:
             print("read failed")
             print(e)

        # end while
    usb.util.dispose_resources(dev)
        
    if reattach:
        dev.attach_kernel_driver(0)
        return 0

if __name__ == '__main__':
    import sys
    sys.exit(main(sys.argv))
